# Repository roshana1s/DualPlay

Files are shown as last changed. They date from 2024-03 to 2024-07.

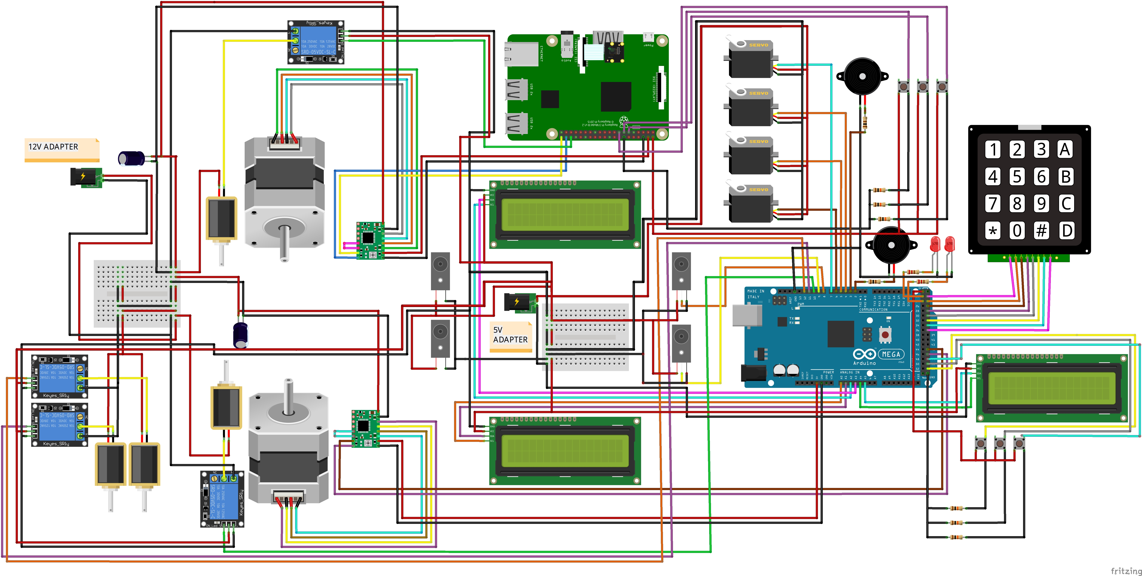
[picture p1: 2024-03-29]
Components and designs/initial_project_components.jpg

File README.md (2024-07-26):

# DualPlay
### The Ultimate Two-Side Air Hockey Experience with an Intelligent Opponent

dualplay_intro

## Introduction 📢
These days, as technology affects every part of our lives, hardware and entertainment combine to create a world of creative possibilities. The main attempt presented by this project is the creation  of an independent physical game that Blends traditional gaming with modern technology.

## Problem in Brief 🚩
1. No human interaction in traditional computer gaming.
   
2. Issues on social dynamics and physical health.
   
3. Traditional physical games require the presence of another player.

## Aim 🎯
Create an interactive multiplayer table game that combines the excitement of air hockey with innovative features.

## Objectives 🎯
1. Design and build the game with two game modes including an autonomous gameplay mode.
   
3. Ensure an enjoyable experience regardless of player availability.

## Game Modes 🎮
### 1. Human vs Human
Two players control paddles using two remotes.

### 2. Human vs AI Player
Human player controls the paddle using a remote and the paddle of the AI player autonomously controlled according to the ball movement by the system.

## Intelligent Features 🧠
1. When the game mode is “Human vs AI”, AI player’s paddle controlled autonomously by tracking the ball and the AI paddle real-time.

2. When a goal is scored, it will detect autonomously, and scores will be updated according to it.

3. After a goal is scored, ball will be redeployed back to the play area autonomously without human intervention.

## Technologies Used 🖥️

### 1. Computer Vision 👁️‍🗨️
  
We implemented a real-time computer vision algorithm using OpenCV in Python to track the colors of the ball and the AI player's paddle. We used HSV color space for this. This allowed us to accurately identify and monitor their positions throughout the game. This computer vision algorithm is executed on Raspberry pi 4 board.



### 2. Arduino Mega and Uno

Arduino Mega controls Green Player side (Human player) and Uno controls Red player side (Human/AI). Game setup LCD, Keypad, Score update LCDs, IR modules, Redeploy servo motors are controlled by Mega. Both boards programmed using C++ and Arduino IDE.

### 3. Serial Communication

We used Serial Communication to communicate between Raspberry pi and two Arduino boards. Arduino boards plugged into raspberry pi through USB ports. 

## Resources Required - Hardware ⚙️

Raspberry pi 4 model B

Arduino Mega

Arduino Uno

Nema 17 Stepper motor *2

180-degree SG90 Servo motor *2

360-degree SG90 continuous Servo motor *2

A4988 Stepper Motor Driver *2

12V 30A power supply

Obstacle Avoidance IR module *2

LCD screen with I2C module *3

Keypad

Limit switch *4

Buck converter *2

Solenoid with Relay module *2

## Resources Required - Software 👨🏽‍💻

Arduino IDE

Geany editor

Tinkercad

SolidWorks

fritzing

## Block Diagram



## Our Team
1. Epasinghe S K
2. Helapalla K O R I
3. Dhananjana R A
4. Nimraka T M N
5. Randinu L L

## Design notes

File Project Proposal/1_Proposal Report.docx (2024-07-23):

CM 1900- Intelligent Machines Inspirational Project

PROJECT PROPOSAL REPORT

Level 01

DualPlay

The Ultimate Two-Side Air Hockey Experience with an Intelligent Opponent

Examiner - Mr. B. H. Sudantha

Submitted by:

225511E - Epasinghe S.K

225520F - Helapalla K.O.R.I

225507X - Dhananjana R.A

225529P - Nimraka T.M.N

225537M - Randinu L.L

Bachelor of Artificial Intelligence

Faculty of Information Technology

University of Moratuwa

# 1. Introduction

These days, as technology affects every part of our lives, hardware and entertainment combine to create a world of creative possibilities. The main attempt presented by this project is the creation of an independent physical game that blends traditional gaming with modern technology. Designed specifically to give players a dynamic experience. Our game named “DualPlay” uses robotics, sensors, and intelligent algorithms to deliver a level of excitement and engagement never seen before.

## 1.1 Problem in Brief

When it comes to the traditional model of computer gaming, it involves playing video games through a computer interface without interacting with other players. Playing these kinds of games for extended periods of time can have negative impacts on social dynamics and physical health. On the other hand, multiplayer, traditional physical games require the presence of another player. In response to these worries, we suggest incorporating the hybrid game "Dual Play," which aims to promote player interaction while also providing independent player-versus-artificial intelligence (AI) features. This invention reduces the limitations that come with playing traditional games by enabling players to engage in gameplay without the need for human players.

## 1.2 Significance of study

This game promotes innovation in gaming technology by providing the player with a hybrid option of playing against a player as well as an autonomous opponent, promoting social interactions while providing the ability to play the game without a human opponent when required. This defines the adaptability of this game to provide entertainment irrespective of the situation. “DualPlay” promotes physical interaction of a player omitting the issues in the traditional computer games.

## 1.3 Aim and Objectives

Aim

The project aims to create an engaging and interactive multiplayer table game that combines the excitement of air hockey with innovative features such as autonomous gameplay modes and customizable gameplay options. The game, titled " DualPlay: The Ultimate Two-Side Air Hockey Experience with an Intelligent Opponent", will provide players with a unique and enjoyable gaming experience that encourages social interaction, strategic thinking, and friendly competition.

Objectives

- To design and build an upgraded version of air hockey game with two game modes: Human vs Human and Human vs Intelligent system.
- To provide an entertaining and enjoyable game that promotes relaxation and mental stress relief.
- To Create a multiplayer experience that encourages social interaction and friendly competition among players.
- To encourage Human Players to Engage in Duels, Challenging and Defeating the Intelligent System player for Ultimate Victory.
- To implement autonomous gameplay modes to accommodate varying numbers of players and ensure an enjoyable experience regardless of player availability.
- To enhance gameplay with visual cues through LCD displays to indicate scores and an integrated sound system for an immersive experience.
- To develop user friendly interfaces for selecting game modes, selecting difficult levels, selecting number of rounds, and keeping track of scores.

# 1. Literature Study

Air Hockey is an interactive and an exciting game for individuals to play during their free time to entertain themselves. It is table game in which two players attempt to score points by using a handheld paddle to shoot a plastic disk across a surface with minimal friction into the opponent's goal [1]. But this game limits at least two players to be present in order to play a game. DualPlay stands out as a unique game which can control one paddle autonomously using computer vision techniques. This can eliminate the limitation where two or more players must be present in order to play a game successfully since only one player can play by controlling the designated paddle while the other paddle functions autonomously.

Players in an Air Hockey game does not receive points or prizes for winning. However, with DualPlay, a player's point scoring may be easily detected and recorded on the LCD screen thanks to the IR break beam sensor. When the game is over, it will also play a victory sound to cheer up the winner.

# 2. Proposed Solution

Our proposed solution, the DualPlay air hockey game, represents a notable advancement from traditional air hockey games. One key feature is the option for human players to compete against either another human player or an intelligent system. This intelligent system utilizes computer vision with OpenCV color tracking and contours detection to dynamically track the ball's movements to get the real-time location of the ball, providing a substantial challenge for human players. Human interaction is facilitated through a user-friendly remote control with three buttons for easy paddle manipulation. Our system sets itself apart with well-organized game modes with different difficulty levels, a real-time score updating system, and innovative ball redeploying mechanisms, establishing the DualPlay system as a distinguished and engaging choice in the air hockey market.

## 2.1 Features of the Proposed Solution

1. Game Initialization: The LED displays show the main menu with the available gameplay modes and difficulty levels.
2. Mode Selection: Player(s) approaches the table and selects their desired gameplay mode using the keypad on the table.

• Available modes include,

- Human vs Intelligent system (1v1)
- Human vs Human (1v1)

• The system will then prompt for the number of points required for a player to win.

3. Player Setup:

• Human vs Intelligent system (1v1) – A human player takes their position at one side of the table and controls their paddle using the corresponding wired remote. The opposing side is autonomously guided by the intelligent system.

• Human vs Human (1v1) – Both human players take their respective positions at the table and control their paddles using individual wired remotes for each side.

4. Ball Placement: The ball will be automatically launched onto the table from one player's side, initiating the start of the game.
5. Game Start:

• Players use their remote controls to move their paddles and start hitting the ball. In cases where the intelligent system is participating, it autonomously guides its paddle by tracking the ball’s position.

• The game begins, and players try to hit the ball into their opponent's goal to score points.

6. Scoring a Goal:

• When a player successfully hits the ball into their opponent's goal, a point is scored.

• The LCD displays update the score, and the sound system emits a celebratory sound to mark the achievement.

7. Ball Reset:

• Following a scored point, the ball is automatically launched onto the table from the side of the player who did not score the point.

8. Score Tracking:

• The LCD displays update the scores for each player in real-time.

• Players can easily see the current score without interrupting the game.

9. Autonomous Gameplay (Human vs Intelligent system (1v1)):

• Here, the system controls one side of the table.

•The Intelligent opponent(system) uses computer vision to track the ball’s position to move the paddle correctly to provide a challenge to the player.

10. Match Completion:

• The game proceeds until one player achieves the predefined winning score.

11. Game Over:

• The game concludes when a player wins the match.

• The LCD displays show the final scores and show who is the winner, and the sound system produces a victory sound.

12. Reset for New Match:

• Players can choose to start a new match, change modes, or end the session.

13. Power Down:

• When the gaming session is complete, the game can be powered down.

• Scores and settings are reset for the next session.

## 2.2 Nature of the Solution

Input

Process

Output

If the system is playing, Track the color of the ball using computer vision algorithms to get the real-time location of the ball and control the intelligent system’s paddle according to the location of the ball. If the human is playing, control the paddle according to user inputs.

Raspberry pi 3 model B

Real-time video capture

Camera

Control the paddle

Belt driven linear paddle system with Nema 17 stepper motor and a solenoid lock

User press push buttons

Push Buttons

(Wired Remote)

Give a signal when the game starts with the game mode and difficulty level or when a round starts

Display game modes, difficulty levels and

Mode selection LCD screen

Arduino Mega

User input

Select the game mode, difficulty level and number of rounds according to the user input.

number of rounds

Keypad

Belt driven linear paddle system with Nema 17 stepper motor and a solenoid lock

User press push buttons

Push Buttons

(Wired Remote)

Control the user's paddle based on input received from the push buttons on the remotes.

Control the paddle

IR Break Beam Sensor

When the ball enters a hole, update the scores on the LCD screens accordingly and activate the buzzer to play the round-winning sound.

Game score updating system with lcd screens and buzzers, and ball redeploy system with servo motors

Whether the ball enters a hole or not

Update scores and redeploy the ball

Figure 01: Block diagram of the input, process, and output

## 2.3 Solution Design

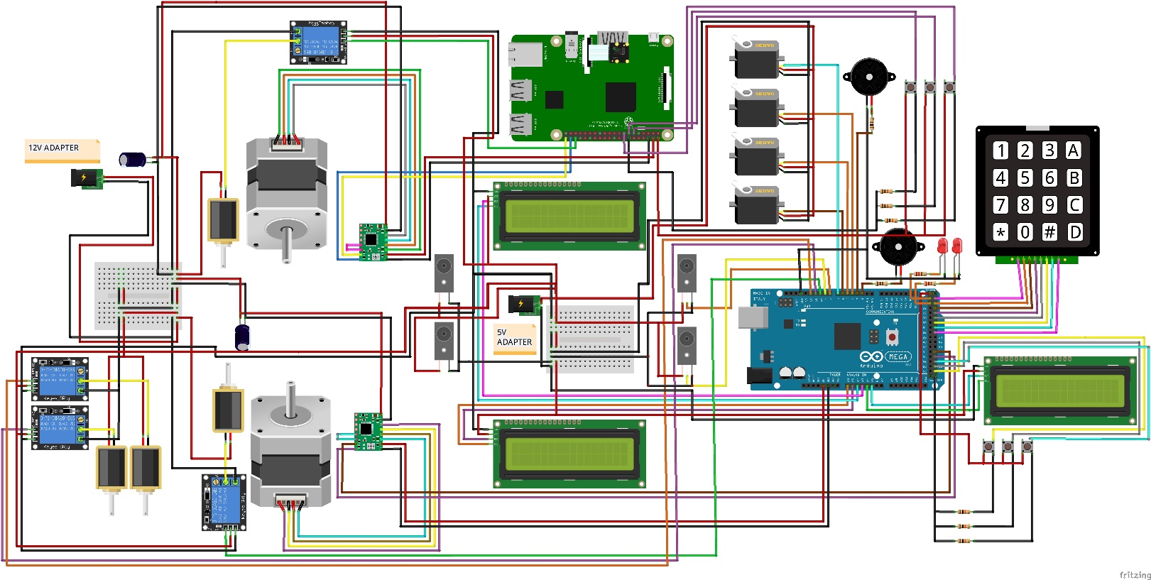
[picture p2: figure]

Figure 02: Connection of components

Scores

Paddle

Ball

Hole

Camera

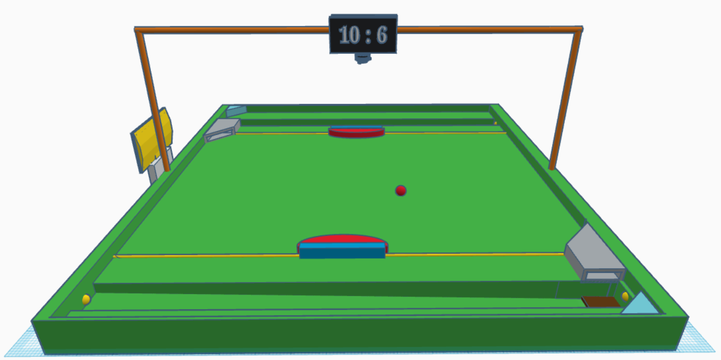
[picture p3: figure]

50 cm

50 cm

IR Break Beam Sensor

Ball Redeploy Mechanism

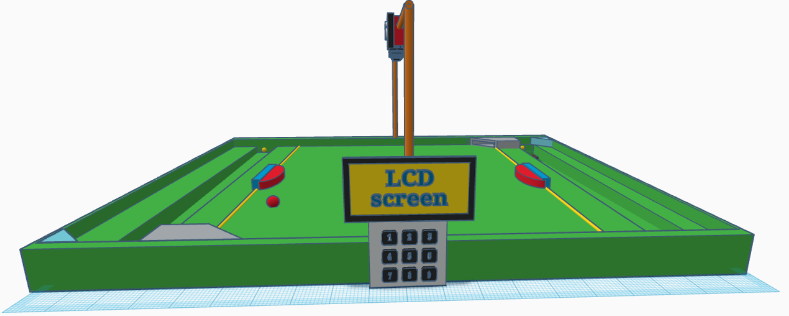
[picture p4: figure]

Mode Selection LCD Screen

Keypad

Figure 03 & 04: A graphical or 3D view of the solution.

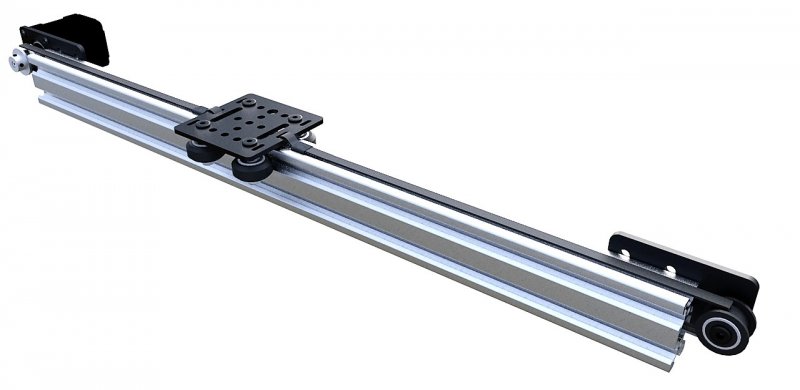
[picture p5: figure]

NEMA 17 stepper motor

Belt

Paddle

Pulley

Figure 05: Paddle move mechanism [2].

## 2.4 Resources

Item name | Price | No. of items | Total (LKR)
Raspberry Pi 3 Model B | 21650 | 1 | 21650
Arduino Mega | 5800 | 1 | 5800
Kingston MicroSD 32GB | 1850 | 1 | 1850
5V 3A Micro USB Power Adapter (Raspberry Pi) | 1050 | 1 | 1050
Tactile Push Button 12x12x7.3mm | 20 | 6 | 120
Servo Motor Plastic Wheel MG90 Full Set | 450 | 2 | 900
Servo Motor Plastic Wheel SG90 Full Set Normal | 380 | 2 | 760
4x4 Matrix Array Keypad | 270 | 1 | 270
1602 16x2 Blue Backlight LCD Display | 360 | 3 | 1080
IIC/I2C/TWI/SPI Serial Interface Board Module Port for 1602 LCD Display PCF8574T | 230 | 3 | 690
Camera Module v1.3 5MP 1080p 720p for Raspberry Pi 3 and 2 | 1350 | 1 | 1350
15-Pin Ribbon Cable 50cm Flex CSI Raspberry Pi Camera | 100 | 1 | 100
17HS8401 NEMA 17 Stepper with wire 0.52Nm (D Shaft 5mm) | 2900 | 2 | 5800
1Kg 3D Printer Filament | 5000 | 1 | 5000
A4988 Stepper Motor Driver for CNC 3D Printer | 350 | 2 | 700
30 Teeth Timing Pulley (5mm Bore) | 560 | 2 | 1120
Brown GT2 6mm Timing Belt (Anti-Slip Toothed Cloth, Rubber with Fiberglass) Per 1m | 430 | 2.5m | 1075
IR Break Beam Sensor 5mm LED | 690 | 2 | 1380
Plywood board (50cm * 50cm) | 1000 | 1 | 1000
Solenoid switch | 1450 | 4 | 5800
2020 t slot aluminum extrusion 1m | 2450 | 1 | 2450
Linear system paddle and supporters | 3000 | 2 | 6000
5VDC 2 Way 2 Channel Relay Module with Coupling Protection | 300 | 2 | 600
SHD2210 Active Piezo Buzzer 3-24VDC 22x10mm | 170 | 2 | 340
12V 20A SMPS Power Supply Metal Casing | 3100 | 1 | 3100
Net Amount | 69390 LKR

## 3.5 Workload Matrix

Registration Number | Assigned Responsibilities
225511E | Program servo motors for ball lift mechanism and program solenoid to strike the ball. (Ball redeploy mechanism in one side) Program two push buttons to get user inputs and program Nema 17 motor for the human play paddle movement according to push button inputs. (One side) Program the mode selection lcd screen to show “A match is ongoing” during a match.
225520F | Program the camera to detect and get the location of the ball and program Nema 17 motor for the system’s paddle movement and program solenoid with relay module to strike the ball for system play. Program two lcd screens, LEDs and buzzers to show the winner and the looser after a match. Make the connection between Arduino and raspberry pi.
225507X | Program one push button to get user input and program solenoid with relay module to strike the ball for the human play according to push button inputs. (One side) Program the keypad and mode selection lcd screen to select game modes, difficulty level and to get number of rounds from the user and program LEDs and buzzers to indicate the start of a match.
225529P | Program two push buttons to get user inputs and program Nema 17 motor for the human play paddle movement according to push button inputs. (One side) Program servo motors for ball lift mechanism and program solenoid to strike the ball. (Ball redeploy mechanism in one side) Program IR beam break sensor in one side.
225537M | Program IR beam break sensors, two lcd screens to display points of players and program buzzers and LEDs to show a point is scored by a player (One side) Program one push button to get user input and program solenoid with relay module to strike the ball for the human play paddle according to push button inputs. (One side)

# 4. References

[1] | "merriam-webster," 2 2 2024. [Online]. Available: https://www.merriam-webster.com/dictionary/air%20hockey.
[2] | "open builds part store," 10 1 2024. [Online]. Available: https://openbuildspartstore.com/v-slot-nema-17-linear-actuator-bundle-belt-driven/ .
[3] | A. TEAM, "arduino.cc," [Online]. Available: https://blog.arduino.cc/2018/10/29/linear-movement-with-arduino-and-3d-printing/. [Accessed 10 1 2024].
[4] | Felipe, "Computer vision engineer," [Online]. Available: https://www.youtube.com/watch?v=eDIj5LuIL4A . [Accessed 27 12 2023].
[5] | "Mechanical Design Masters," [Online]. Available: https://youtu.be/ve9M8d6KfdI?si=8PxCvQbe-xPVnI0p. [Accessed 20 12 2023].
[6] | "OpenCV," [Online]. Available: https://docs.opencv.org/3.4/df/d9d/tutorial_py_colorspaces.html. [Accessed 27 12 2023].
[7] | "OpenCV," [Online]. Available: https://docs.opencv.org/3.4/da/d97/tutorial_threshold_inRange.html. [Accessed 27 12 2023].
[8] | "OpenCV," [Online]. Available: https://docs.opencv.org/4.x/d3/d05/tutorial_py_table_of_contents_contours.html. [Accessed 27 12 2023].

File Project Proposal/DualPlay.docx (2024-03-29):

CM 1900 - Intelligent Machines Inspirational Project

B.Sc.(Hons) Artificial Intelligence

Group 01

Admission No | Name
225511E | Epasinghe S.K
225520F | Helapalla K.O.R.I
225507X | Dhananjana R.A
225529P | Nimraka T.M.N
225537M | Randinu L.L

DualPlay

The Ultimate Two-Side Air Hockey Experience with an Intelligent Opponent

# Introduction:

The project aims to create an engaging and interactive multiplayer table game that combines the excitement of air hockey with innovative features such as autonomous gameplay modes and customizable gameplay options. The game, titled " DualPlay: The Ultimate Two-Side Air Hockey Experience with an Intelligent Opponent", will provide players with a unique and enjoyable gaming experience that encourages social interaction, strategic thinking, and friendly competition.

## Game Modes:

- Human vs Intelligent player(system)
- Human vs Human

# System objectives:

- Provide an entertaining and enjoyable game that promotes relaxation and mental stress relief.
- Create a multiplayer experience that encourages social interaction and friendly competition among players.
- Encourage Human Players to Engage in Duels, Challenging and Defeating the Intelligent System player for Ultimate Victory
- Implement autonomous gameplay modes to accommodate varying numbers of players and ensure an enjoyable experience regardless of player availability.
- Enhance gameplay with visual cues through LCD displays to indicate scores and an integrated sound system for an immersive experience.
- Develop user-friendly interfaces for selecting gameplay modes and keeping track of scores.

# How The Game Works:

The game supports multiple play modes to cater to different numbers of players.

1. Game Initialization:

- The LED displays show the main menu with the available gameplay modes.

2. Mode Selection:

- Player(s) approach the table and select their desired gameplay mode using the buttons on the table.
- Available modes include,
    - Human vs Intelligent system (1v1)
    - Human vs Human (1v1)
- The system will then prompt for the number of points required for a player to win.

3. Player Setup:

- Human vs Intelligent system (1v1) – A human player takes their position at one side of the table and controls their paddle using the corresponding wired remote. The opposing side is autonomously guided by the intelligent system.
- Human vs Human (1v1) – Both human players take their respective positions at the table and control their paddles using individual wired remotes for each side.

4. Ball Placement:

- The ball will be automatically launched onto the table from one player's side, initiating the start of the game.

5. Game Start:

- Players use their remote controls to move their paddles and start hitting the ball. In cases where the intelligent system is participating, it autonomously guides its paddle by tracking the ball’s position.
- The game begins and players try to hit the ball into their opponent's goal to score points.

6. Scoring a Goal:

- When a player successfully hits the ball into their opponent's goal, a point is scored.
- The LCD displays update the score, and the sound system emits a celebratory sound to mark the achievement.

7. Ball Reset:

- Following a scored point, the ball is automatically launched onto the table from the side of the player who did not score the point.

8. Score Tracking:

- The LCD displays update the scores for each player in real-time.
- Players can easily see the current score without interrupting the game.

9. Autonomous Gameplay (Human vs Intelligent system (1v1)):

- Here, the system controls one side of the table.
- The Intelligent opponent(system) uses computer vision to track the ball’s position to move the paddle correctly to provide a challenge to the player.

10. Match Completion:

- The game proceeds until one player achieves the predefined winning score.

11. Game Over:

- The game concludes when a player wins the match.
- The LCD displays show the final scores and show who is the winner, and the sound system produces a victory sound.

12. Reset for New Match:

- Players can choose to start a new match, change modes, or end the session.

13. Power Down:

- When the gaming session is complete, the game can be powered down.
- Scores and settings are reset for the next session.

# System Components and Sensors

Item name | Price | No. of items | Total
Raspberry Pi 3 Model B * | 21650 | 1 | 21650
Arduino Mega | 5800 | 1 | 5800
Kingston MicroSD 32GB | 1900 | 1 | 1900
5V 3A Micro USB Power Adapter (Raspberry Pi) | 1050 | 1 | 1050
DS-212 Green 16mm Round Metal Push Button Momentary Switch | 100 | 4 | 400
DS-212 Red 16mm Round Metal Push Button Momentary Switch | 100 | 2 | 200
Continuous Rotation SG90 Servo Motor Plastic Wheel Full Set Normal (360 degrees) | 350 | 4 | 1400
4x3 Matrix Array Keypad Switch Module | 750 | 1 | 750
1602 16x2 Blue Backlight LCD Display | 360 | 3 | 1080
IIC/I2C/TWI/SPI Serial Interface Board Module Port for 1602 LCD Display PCF8574T | 230 | 3 | 690
Camera Module v1.3 5MP 1080p 720p for Raspberry Pi 3 and 2 | 1350 | 1 | 1350
15-Pin Ribbon Cable 50cm Flex CSI Raspberry Pi Camera | 100 | 1 | 100
17HS8401 NEMA 17 Stepper with wire 0.52Nm (D Shaft 5mm) | 2900 | 2 | 5800
Creality Ender EN-PLA White 1.75mm 1Kg 3D Printer Filament | 5600 | 1 | 5600
A4988 Stepper Motor Driver for CNC 3D Printer | 350 | 2 | 700
GT2 20T 20 Teeth Timing Pulley (5mm Bore) 20TB5W6 Silver | 180 | 2 | 360
Brown GT2 6mm Timing Belt (Anti-Slip Toothed Cloth, Rubber with Fiberglass) Per 1m | 430 | 3m | 1290
IR Break Beam Sensor 5mm LED | 690 | 2 | 1380
Plywood board | 2000 | 1 | 2000
Solenoid switch | 1000 | 2 | 2000
Net Amount | 49650

# System Functions

## 1. Wired Remotes

Each wired remote is equipped with three push buttons:

    - One to move the paddle to the left.
    - One to move the paddle to the right.
    - One to push the ball.

## 2. Table (Main System)

### Ball Tracking

When the Intelligent system is in play, the system employs computer vision algorithms from the OpenCV library to track the real-time color of the ball. By utilizing computer vision algorithms to track the ball's color, the system can dynamically identify the ball's position in real-time, allowing the system to adjust the paddle's movement accordingly.

### Paddle Move Mechanism

The paddle move mechanism utilizes a NEMA 17 stepper motor paired with an A4988 driver, and a 20-tooth timing pulley connected to a timing belt. As the stepper motor rotates, it drives the timing pulley, causing linear motion in the attached timing belt. This motion is then transferred to the air hockey paddle, enabling precise and controlled movement on the playing surface.


Belt

Paddle

Pulley

NEMA 17 stepper motor

An example for paddle move mechanism (actual design may differ)

### Ball Pushing Mechanism

The pushing mechanism involves a continuous servo motor equipped with a rack and pinion gear system. This setup transforms the rotational motion of the servo into linear motion. When activated, the servo engages the rack and pinion gears, swiftly converting rotational energy into a sudden linear push. This mechanism is specifically designed to impart a quick and precise force to propel the ball during gameplay.

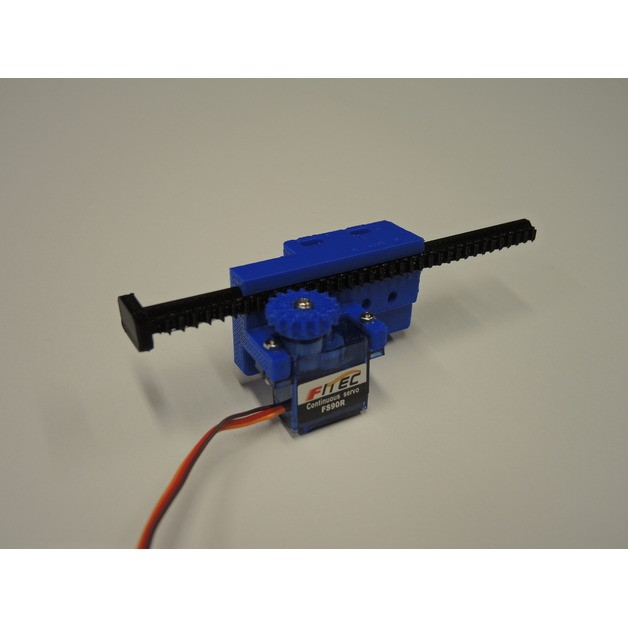
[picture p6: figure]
Jual Linear Servo Actuators - Kota Bekasi - Ednic Indonesia | Tokopedia

Rack

Servo motor

Pinion gear

An example for Ball pushing mechanism (actual design may differ)

### Score tracking

In our scoring system, an IR Break Beam Sensor is employed to detect whether the ball has entered the goal. When a player scores a point, the IR Break Beam Sensor registers this event and sends the signal to a Raspberry Pi. Subsequently, the Raspberry Pi communicates the scoring information to an Arduino Uno board, ensuring real-time score updates during gameplay.

### Ball Redeploy Mechanism

A built-in inclined plane in the hole, guides the ball to the right corner within the goal. Using a servo motor and a rack and pinion mechanism, the ball is lifted to table level. Once elevated, the same mechanism generates a pushing effect, redeploying the ball back into the play area. This simple yet effective system ensures a smooth and consistent ball redeployment process after scoring.

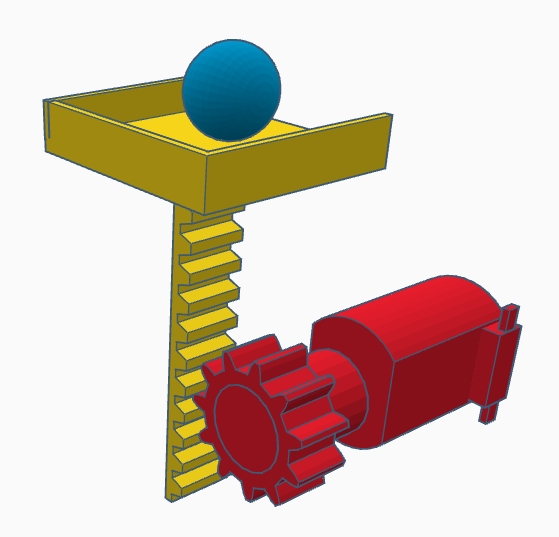
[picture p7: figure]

continuous Servo motor

(static position)

An example for Ball lifting mechanism (actual design may differ)

# Block Diagram

Camera Module

Push Buttons

LCD screens

(scores)

12C modules

Stepper Motors

Raspberry PI

Arduino UNO

Buzzers

A4988

LEDs

Servo motors

Mode selection LCD screen

12C module

IR Break Beam Sensors

Keypad

# Design

Scores


Camera

Ball Redeploy Mechanism

Hole

Ball

Paddle

IR Break Beam Sensor


Mode Selection LCD Screen

Keypad

# References

OpenCV Documentation

- https://docs.opencv.org/3.4/df/d9d/tutorial_py_colorspaces.html
- https://docs.opencv.org/3.4/da/d97/tutorial_threshold_inRange.html
- https://docs.opencv.org/4.x/d3/d05/tutorial_py_table_of_contents_contours.html

OpenCV YouTube Tutorial

- https://www.youtube.com/watch?v=eDIj5LuIL4A

Mechanisms for converting Rotational Motion into Linear

- https://youtu.be/ve9M8d6KfdI?si=8PxCvQbe-xPVnI0p

Other Links –

- https://blog.arduino.cc/2018/10/29/linear-movement-with-arduino-and-3d-printing/
- https://openbuildspartstore.com/v-slot-nema-17-linear-actuator-bundle-belt-driven/

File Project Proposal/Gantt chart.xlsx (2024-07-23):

Task | Start Date | End Date | Duration
Identify problem and propose solution | 2023-12-22 | 2023-12-29 | 7
Conduct research | 2023-12-30 | 2024-01-04 | 5
Finalize project design and obtain approval | 2024-01-05 | 2024-01-12 | 7
Develop computer vision algorithm for ball tracking | 2024-01-01 | 2024-01-20 | 19
Establish connection between Raspberry Pi and Arduino | 2024-02-07 | 2024-02-14 | 7
Implement LCD screen and keypad for game setup | 2024-03-13 | 2024-03-30 | 17
Implement linear actuator | 2024-02-14 | 2024-03-20 | 35
Integrate solenoid with relay for ball striking | 2024-02-16 | 2024-02-23 | 7
Develop remote input for solenoid control | 2024-02-23 | 2024-03-02 | 8
Develop remote input for linear actuator (paddle) control | 2024-03-16 | 2024-04-10 | 25
Develop autonomous solution for solenoid control | 2024-05-02 | 2024-05-10 | 8
Develop autonomous solution for linear actuator control | 2024-04-06 | 2024-04-22 | 16
Implement goal counter | 2024-04-06 | 2024-04-22 | 16
Integrate buzzers and LEDs | 2024-04-22 | 2024-04-25 | 3
Implement ball redeploy mechanism | 2024-05-01 | 2024-05-10 | 9
Finalize 3D parts design and initiate printing | 2024-04-25 | 2024-05-10 | 15
Implement second linear actuator (paddle) and solenoid | 2024-04-22 | 2024-05-10 | 18
Assemble all parts and complete project | 2024-04-22 | 2024-06-02 | 41

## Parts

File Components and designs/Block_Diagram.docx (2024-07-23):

If the AI player is playing, Track the color of the ball and paddle using computer vision algorithms to get the real-time location of the ball and the paddle.

Raspberry pi 4 model B

Real-time video capture

Camera

Control the paddle

Arduino Uno

Get signals from raspberry pi according to locations of the ball and the paddle and control AI player’s paddle.

Belt driven linear paddle system with Nema 17 stepper motor and a solenoid lock

User press push

buttons

Control the user's paddle based on input received from the push buttons on the remotes.

Push Buttons

(Wired Remote)

Control the paddle

Game setup LCD Screen

number of rounds

Display game modes, difficulty levels and

Arduino Mega

User input

Select the game mode and enter the number of rounds according to the user input.

Keypad

Belt driven linear paddle system with Nema 17 stepper motor and a solenoid lock

User press push buttons

Push Buttons

(Wired Remote)

Control the user's paddle based on input received from the push buttons on the remotes.

Control the paddle

IR Module

When the ball enters a hole, update the scores on the LCD screens accordingly and activate the buzzer and activate Redeploy mechanism.

Game score updating system with lcd screens and buzzer, and ball redeploy system with servo motors

Whether the ball enters a hole or not

Update scores and redeploy the ball

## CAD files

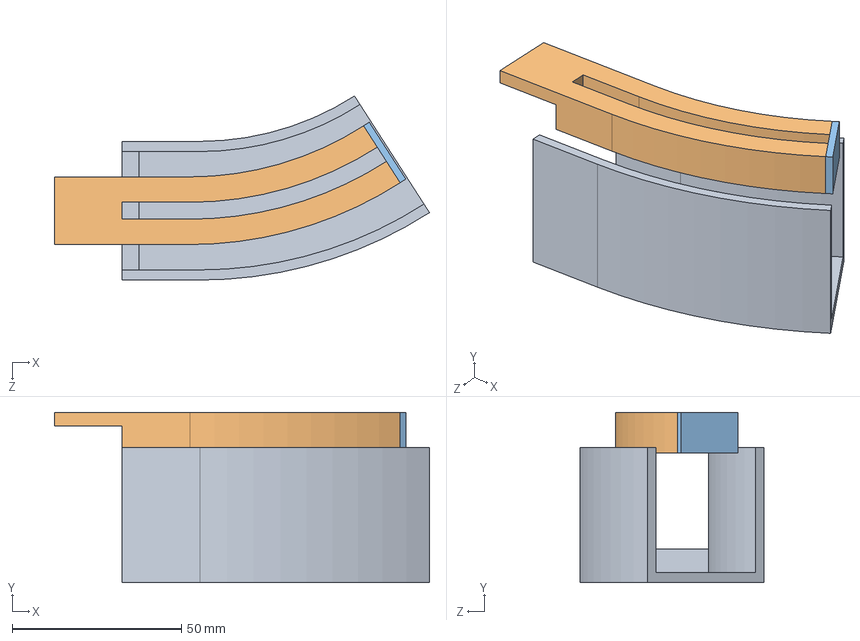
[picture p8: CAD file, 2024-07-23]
3d design/Redeploy-Push/Assem1.SLDASM
110.9 x 50.4 x 54.4 mm

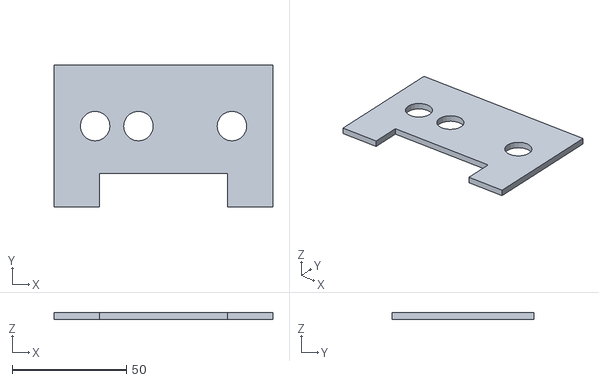
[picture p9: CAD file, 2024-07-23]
3d design/controller/controller1.stl
96.0 x 62.5 x 3.00

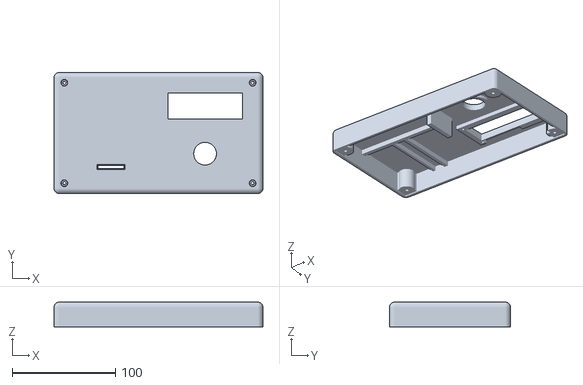
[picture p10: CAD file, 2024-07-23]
3d design/Game_Setup_LCD_and_Keypad/keypad cover.stl
202.0 x 117.0 x 24.0

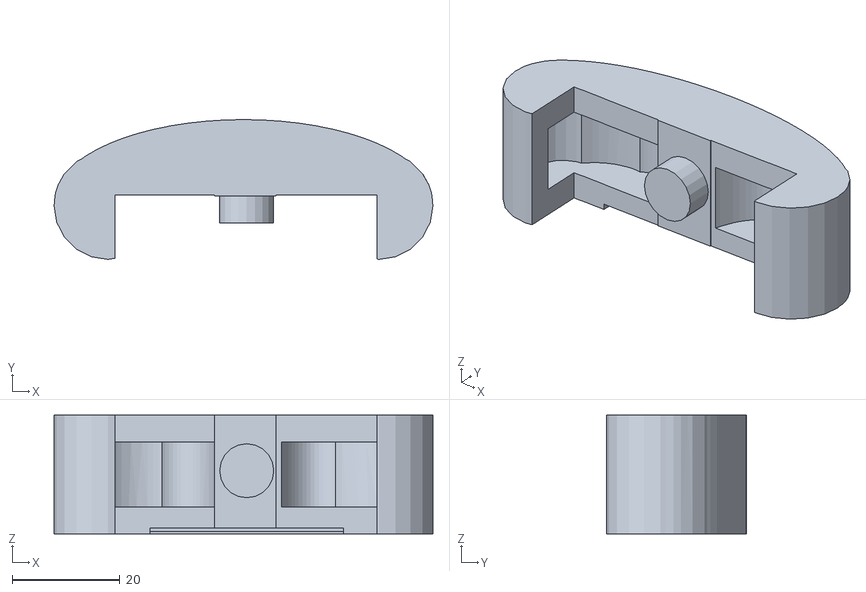
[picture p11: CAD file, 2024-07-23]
3d design/Paddle/strike1.stl
70.2 x 25.9 x 22.0

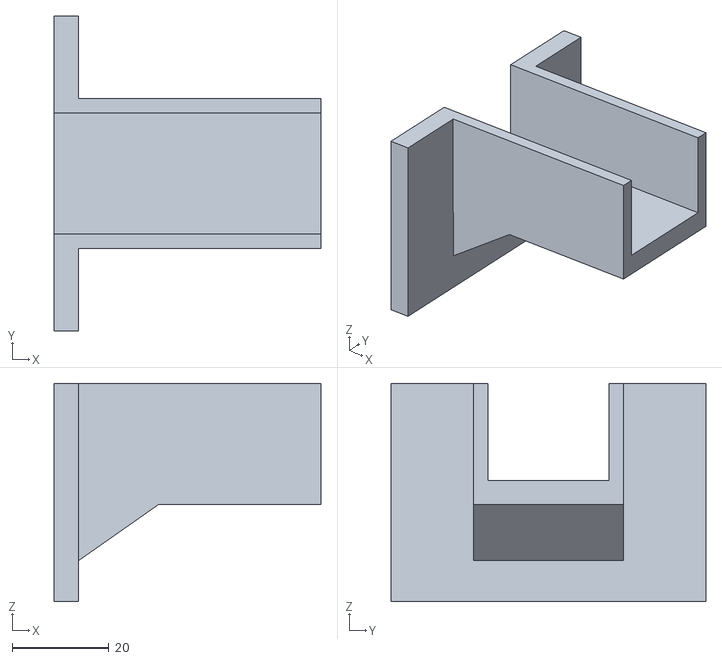
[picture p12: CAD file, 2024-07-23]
3d design/Rail_Support/railSup.stl
55.0 x 65.0 x 45.0

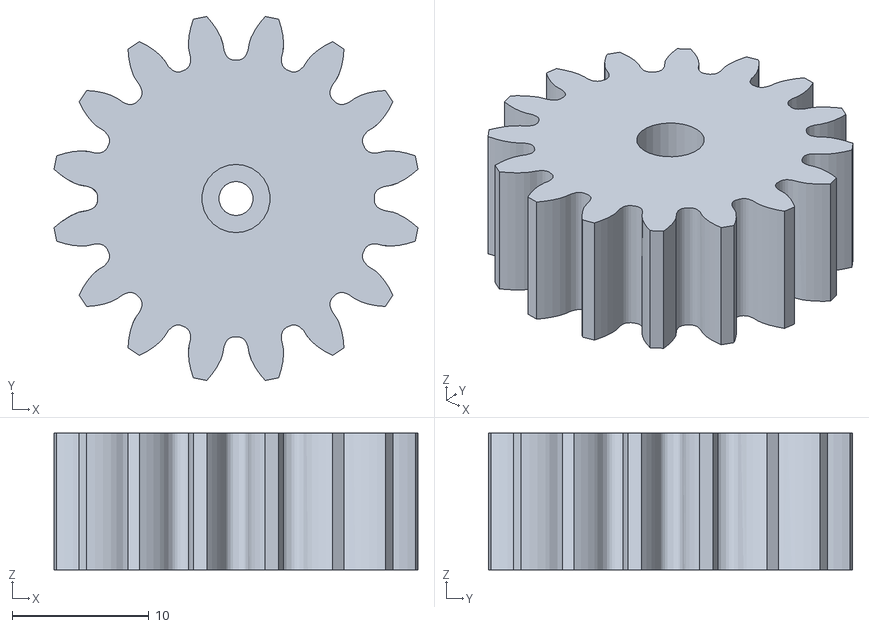
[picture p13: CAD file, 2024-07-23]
3d design/Redeploy-Lift/part5.stl
26.7 x 26.7 x 10.0

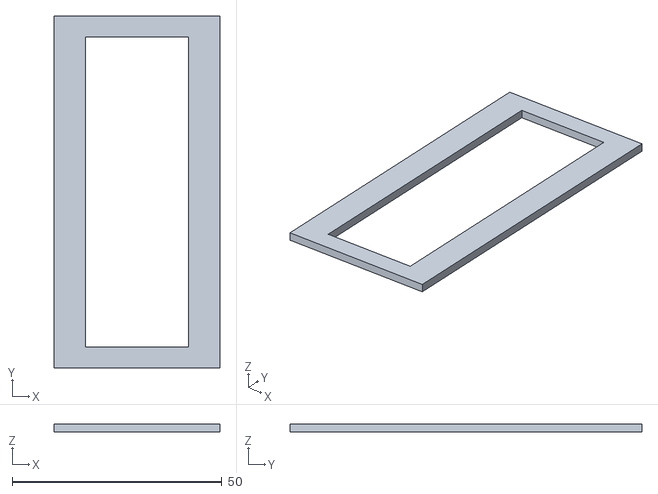
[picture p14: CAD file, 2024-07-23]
3d design/Score_Update_LCD/display2.stl
39.5 x 84.0 x 2.00

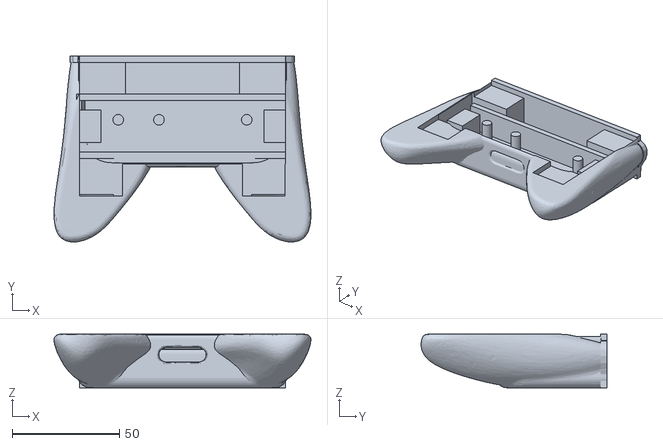
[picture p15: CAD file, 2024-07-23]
3d design/controller/controller2.stl
120.0 x 86.8 x 25.0

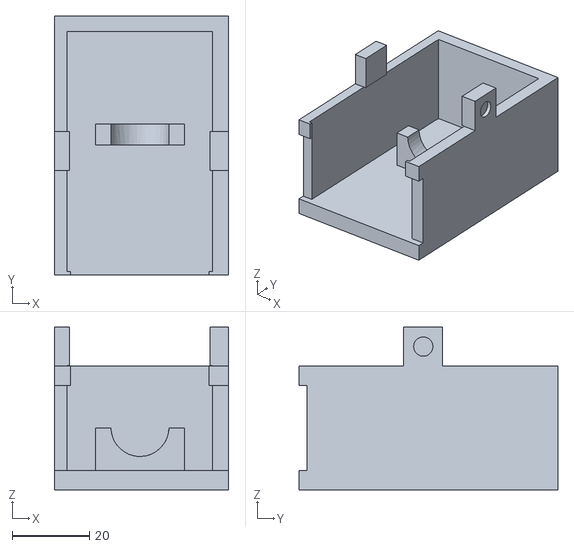
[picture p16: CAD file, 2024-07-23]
3d design/Paddle/paddle2.stl
45.0 x 66.9 x 42.0

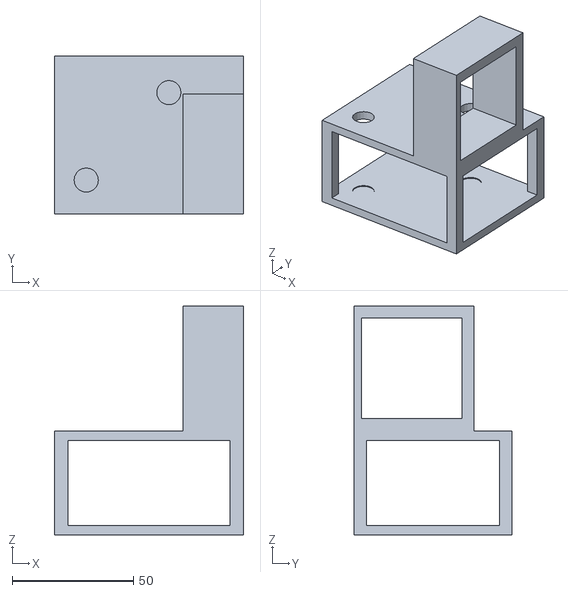
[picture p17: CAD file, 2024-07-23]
3d design/Rail_Support/support1.stl
78.0 x 65.0 x 94.5

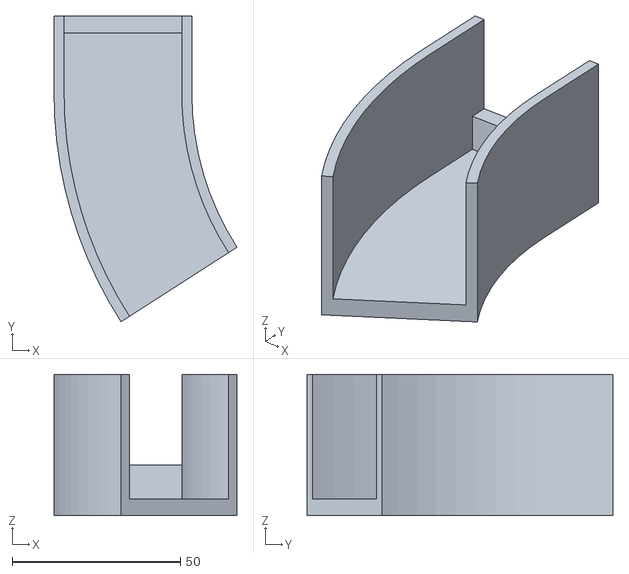
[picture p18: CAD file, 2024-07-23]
3d design/Redeploy-Lift/PART9.stl
54.4 x 90.9 x 42.0

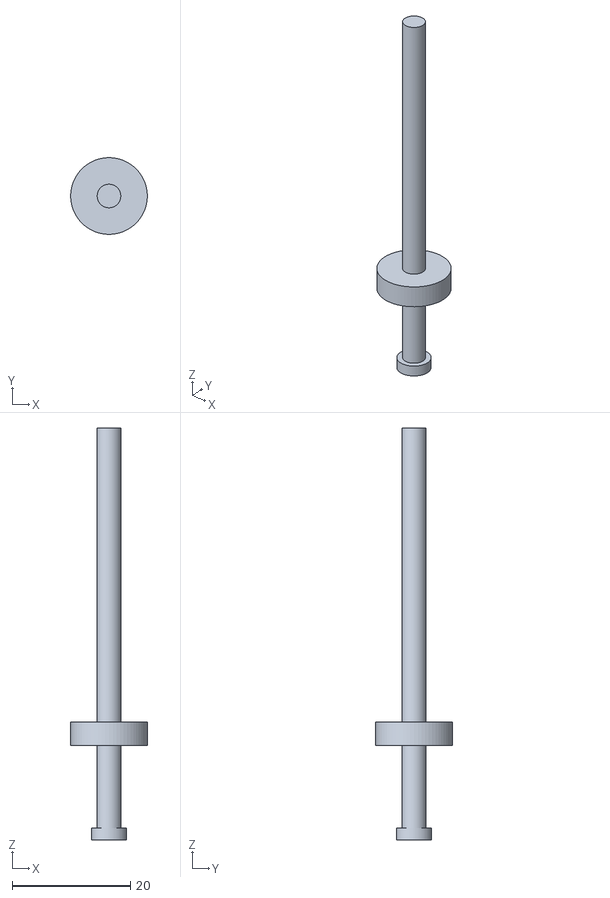
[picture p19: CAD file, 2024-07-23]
3d design/Redeploy-Push/PART6.stl
13.0 x 13.0 x 69.8

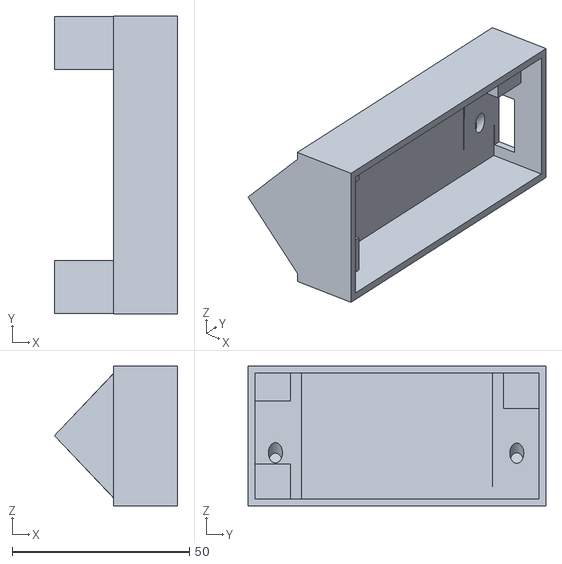
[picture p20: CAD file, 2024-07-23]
3d design/Score_Update_LCD/display1.stl
34.8 x 84.0 x 39.5

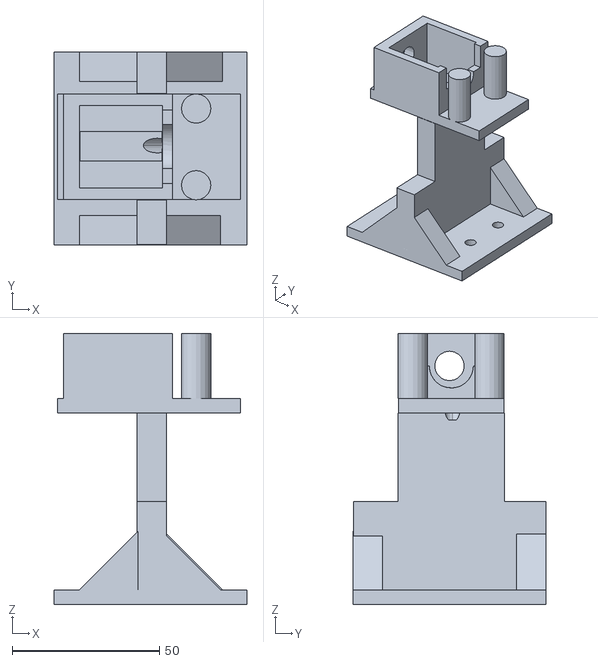
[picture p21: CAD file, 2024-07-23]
3d design/Paddle/paddle1.stl
65.5 x 65.6 x 92.0

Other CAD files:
3d design/Redeploy-Lift/lift3.stl
3d design/Redeploy-Push/PART2.stl
3d design/Paddle/strike11.stl
3d design/Redeploy-Lift/lift2.stl
3d design/Redeploy-Lift/PART9-1.stl
3d design/Redeploy-Lift/lift1.stl
3d design/Redeploy-Lift/lift4.stl
3d design/Redeploy-Lift/part4.stl
3d design/Redeploy-Push/PART1.stl
3d design/Redeploy-Push/PART3.stl
3d design/Redeploy-Push/PART4.stl
3d design/Redeploy-Push/PART5.stl
3d design/Redeploy-Push/PART7.STL
3d design/Redeploy-Push/PART8.stl
3d design/Redeploy-Push/Part7.SLDPRT
3d design/Redeploy-Push/Part8.SLDPRT
3d design/Redeploy-Push/Part9.SLDPRT

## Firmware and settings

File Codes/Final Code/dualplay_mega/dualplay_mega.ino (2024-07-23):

// DualPlay 

// Code for arduino Mega

#include <LiquidCrystal_I2C.h>
#include <Keypad.h>
#include <Servo.h>

// Obstacle Avoidance Sensor IR Infrared Module pins 
const int ir_red = 5, ir_green = 6;

// initial values and declare variables
int d, Nrounds, round_input, gm, com, gp, score, redScore = 0, greenScore = 0;

// A4988 motor driver direction and step pins
const int dirPin = 46, stepPin = 3;

const int stepsPerRevolution = 70;
const int debounceDelay = 50; // Debounce delay in milliseconds

// Pins for the remote
const int leftMove = 10, rightMove = 11, solenoid = 8;

// Pins for the relay and two limit switches
const int relay = 9, leftStop = 22, rightStop = 24;

// Pin for the active buzzer
const int buzzer = 2;

// Variables to messure time
unsigned long currentTime, b2Time = 0, b1Time = 0, solenoidTime = 0;

// delay between two steps of stepper motor
int del = 400, ir_value;

// 2D array for the 4x3keypad matrix
char keys[4][3] = {
	{'1','2','3'},
	{'4','5','6'},
	{'7','8','9'},
	{'*','0','#'}
};

// define row pins and column pins of the keypad
byte rowPins[4] = {28,30,32,34}; 
byte colPins[3] = {38,40,44}; 

//46 
// map keys
Keypad kpd = Keypad( makeKeymap(keys), rowPins, colPins, 4, 3 );


// define three lcd screens
LiquidCrystal_I2C lcd_gameSetup(0x27, 16, 2);
LiquidCrystal_I2C lcd_green(0x25 ,16, 2);
LiquidCrystal_I2C lcd_red(0x26, 16, 2);

// define four servo motors
Servo lift_green;
Servo push_green;
Servo lift_red;
Servo push_red;

/////////////////////////////////////////////////////////////////

// Function for Active buzzer
void sound_buzzer(){
    digitalWrite(buzzer, HIGH);
    delay(300);           
    digitalWrite(buzzer, LOW);
}

// welcome message
void wc_msg(){
    lcd_gameSetup.clear();
    lcd_gameSetup.setCursor(3, 0);
    lcd_gameSetup.print("Welcome to ");
    lcd_gameSetup.setCursor(4, 1);
    lcd_gameSetup.print("dualPlay"); 
}

// Select Play or Not
int gameplay(){
  lcd_gameSetup.clear();
  lcd_gameSetup.setCursor(0, 0);
  lcd_gameSetup.print("1)start");
  lcd_gameSetup.setCursor(0, 1);
  lcd_gameSetup.print("2)switch off");
  char key;
  while(1){
    key = kpd.getKey();
    if(key=='1' || key=='2'){
         sound_buzzer();
         break;
    }
  }
  return key-'0';
}

// Select the game mode
int game_mode(){
    lcd_gameSetup.clear();
    lcd_gameSetup.setCursor(2, 0);
    lcd_gameSetup.print("Select the");
    lcd_gameSetup.setCursor(3, 1);
    lcd_gameSetup.print("Game Mode");
    delay(1000);
    lcd_gameSetup.clear();
    lcd_gameSetup.setCursor(0, 0);
    lcd_gameSetup.print("1.Human vs Human");
    lcd_gameSetup.setCursor(0, 1);
    lcd_gameSetup.print("2.Human vs AI");
    char key;
    while(1){
      key = kpd.getKey();
      if(key=='1' || key=='2') {
        sound_buzzer();
        break;
      }
    }
    lcd_gameSetup.clear();
    if(key == '1'){
      lcd_gameSetup.setCursor(1, 0);
      lcd_gameSetup.print("You Selected");
      lcd_gameSetup.setCursor(1, 1);
      lcd_gameSetup.print("Human vs Human");
  }
  else if(key == '2'){
    lcd_gameSetup.setCursor(1, 0);
    lcd_gameSetup.print("You Selected");
    lcd_gameSetup.setCursor(1, 1);
    lcd_gameSetup.print("Human vs AI");
  }
  delay(1000);
  return key-'0';
}

// Select Number of Rounds
int rounds(){
  lcd_gameSetup.clear();
  lcd_gameSetup.setCursor(0, 0);
  lcd_gameSetup.print("{No of rounds}#");
  lcd_gameSetup.setCursor(0, 1);
  lcd_gameSetup.print("Enter(max 99): ");
  lcd_gameSetup.setCursor(14, 1);

  String number = "";
  while(1){
    char key;
    key =  kpd.getKey();
    if(isdigit(key) && number.length()<2){
      sound_buzzer();
      if(key == '0' && number.length()==0){
        continue;
      }else{
        lcd_gameSetup.print(key);
        number += String(key);
      }
    }
    else if(key=='#' && number.length()>=1){
      sound_buzzer();
      lcd_gameSetup.clear();
      lcd_gameSetup.setCursor(0, 0);
      lcd_gameSetup.print("No of rounds:");
      lcd_gameSetup.setCursor(13, 0);
      lcd_gameSetup.print(number);
      lcd_gameSetup.setCursor(0, 1);
      lcd_gameSetup.print("Game is ongoing");
      return number.toInt();
    }
    else if(key=='*' && number.length()>=1){
      sound_buzzer();
      number = number.substring(0, number.length() - 1);
      lcd_gameSetup.clear();
      lcd_gameSetup.setCursor(0, 0);
      lcd_gameSetup.print("{No of rounds}#");
      lcd_gameSetup.setCursor(0, 1);
      lcd_gameSetup.print("Enter(max 99): ");
      lcd_gameSetup.setCursor(14, 1);
      lcd_gameSetup.print(number);
    }
  }
}

// game setup function
void gameSetup(){
  gp = gameplay();
  if(gp==1){
    wc_msg();
    delay(1000);
    gm = game_mode();
    Nrounds = rounds();
    com = gm;
  }
  else{
    com = 0;
    lcd_gameSetup.clear();
    lcd_gameSetup.setCursor(1, 0);
    lcd_gameSetup.print("Switching Off!!!!");
    delay(4000);

    lcd_gameSetup.clear();
    lcd_green.clear();
    lcd_red.clear();

    lcd_gameSetup.setCursor(1, 0);
    lcd_gameSetup.print("GoodBye !!");
    lcd_green.setCursor(1, 0);
    lcd_green.print("GoodBye !!");
    lcd_red.setCursor(1, 0);
    lcd_red.print("GoodBye !!");
  }
}

// Function to clear serial buffer
void ClearSerial(){
  while (Serial.available() > 0) {
    Serial.read();
  }
}

// Function to check whther ir beam is intact or not
int breakbeam() { 
  // Small delay to avoid flooding the Serial Monitor
    if (!digitalRead(ir_red)) {
        // Serial.println("IR Beam is Broken - red");
        return 1;
    }else if (!digitalRead(ir_green)) {
        // Serial.println("IR Beam is Broken - Green");
        return 2;
   }else {
        // Serial.println("IR Beam is Intact");
        return 0;
    }
}

// Function to update score
void scoreDisplay(int red, int green){
    lcd_green.setCursor(0, 1);
    lcd_green.print("red: ");
    lcd_green.print(red);
    lcd_green.print(" Green: ");
    lcd_green.print(green);

    lcd_red.setCursor(0, 1);
    lcd_red.print("red: ");
    lcd_red.print(red);
    lcd_red.print(" Green: ");
    lcd_red.print(green);
}

void score_update(int score) {
    if (score == 1) {
        greenScore += 1;
    } else if (score == 2) {
        redScore += 1;
    }
    scoreDisplay(redScore, greenScore);

}

// Function to identify Button press for the paddle
void handleButtons()
{
  static unsigned long lastDebounceTime = 0;
  static int lastButtonState1 = HIGH;
  static int lastButtonState2 = HIGH;

  int buttonState1 = digitalRead(rightMove);
  int buttonState2 = digitalRead(leftMove);

  if (buttonState1 != lastButtonState1) {
    lastDebounceTime = currentTime;
  }

  if (buttonState2 != lastButtonState2) {
    lastDebounceTime = currentTime;
  }

  if ((currentTime - lastDebounceTime) > debounceDelay) {
    if (buttonState1 == LOW && digitalRead(rightStop)) {
      digitalWrite(dirPin, HIGH);
      runMotor();
    }
    if (buttonState2 == LOW && digitalRead(leftStop)) {
      digitalWrite(dirPin, LOW);
      runMotor();
    }
  }

  lastButtonState1 = buttonState1;
  lastButtonState2 = buttonState2;
}

// Function to run paddle
void runMotor()
{
  for (int x = 0; x < stepsPerRevolution; x++) {
    digitalWrite(stepPin, HIGH);
    delayMicroseconds(del);
    digitalWrite(stepPin, LOW);
    delayMicroseconds(del);
  }
}

// Function to identify button input to solenoid and strike the ball
void handleSolenoid()
{
  if (currentTime - solenoidTime >= 10) {
    solenoidTime = currentTime;
    if (digitalRead(solenoid) == LOW) {
      digitalWrite(relay, LOW);
    } else {
      digitalWrite(relay, HIGH);
    }
  }
}

// Function for the redeploy mechanism in the green side
void greenDeploy() {
  for (int pos = 90; pos <= 180; pos += 2) {
    push_green.write(pos);
    delay(5);  // Wait for 5 milliseconds for the servo to move
  }
  
  lift_green.write(75);  // Rotate counterclockwise
  delay(1600);     // Rotate for 2 seconds
  
  lift_green.write(90);  // Stop the servo
  delay(500);     // Wait for 1 second
  
  // Move the push_green servo back to 10 degrees
  push_green.write(90);
  delay(500);
  lift_green.write(110); // Rotate clockwise
  delay(1200);     // Rotate for 2 seconds
  
  lift_green.write(90);  // Stop the servo
}

// Function for the redeply mechanism in the red side
void redDeploy(){
  for (int pos = 85; pos <= 180; pos = pos + 1) {
    push_red.write(pos); // Sets 'push_red' servo to current 'pos' position
    delay(5);        // Waits for 5 milliseconds
  }

  lift_red.write(80);  // Rotate counterclockwise at full speed
  delay(1500);       // Rotate for 2 seconds
  lift_red.write(90); // Stop the servo
  push_red.write(85);
  delay(1000);
  lift_red.write(98); // Rotate clockwise at full speed
  delay(900);        

  lift_red.write(90);
}

// Function for run redeploy
void redeploy(int value){
  if(value==1){
    redDeploy();
  }
  else if(value==2){
    greenDeploy();
  }
}

// Function to get starting positions
void startPaddle(int value){
  if(value==1){
    digitalWrite(dirPin, LOW);
    while(digitalRead(leftStop)) runMotor();
    Serial.println("left");
  }else if(value==2){
    digitalWrite(dirPin, HIGH);
    while(digitalRead(rightStop)) runMotor();
    Serial.println("right");
  }
}

///////////////////////////////////////////////////////////////////

void setup()
{
	Serial.begin(115200);
  while(!Serial);

  pinMode(ir_red, INPUT);
  pinMode(ir_green, INPUT);
  pinMode(stepPin, OUTPUT);
  pinMode(dirPin, OUTPUT);
  pinMode(relay, OUTPUT);
  pinMode(leftMove, INPUT_PULLUP); 
  pinMode(rightMove, INPUT_PULLUP); 
  pinMode(rightStop, INPUT_PULLUP); 
  pinMode(leftStop, INPUT_PULLUP); 
  pinMode(solenoid, INPUT_PULLUP); 
  pinMode(buzzer, OUTPUT);

  digitalWrite(relay, HIGH); // switch off relay at first

  lift_green.attach(14);  // Attaches the servo object 'lift_green' to pin 10
  push_green.attach(15);   // Attaches the servo object 'push_green' to pin 9
  push_green.write(10);   // Initialize push_green servo to starting position
  lift_green.write(90);

  lift_red.attach(50);  // Attaches the servo object 'lift_red' to pin 10
  push_red.attach(52);   // Attaches the servo object 'push_red' to pin 9
  lift_red.write(90);

  lcd_gameSetup.begin();
	lcd_gameSetup.backlight();
  lcd_green.begin();
	lcd_green.backlight();
  lcd_red.begin();
	lcd_red.backlight();

  lcd_green.setCursor(4,0);
  lcd_green.print("DualPlay");
  lcd_red.setCursor(4,0);
  lcd_red.print("DualPlay");

  // wait until for the signal from raspberry pi (to identify the correct port)
  String s;
  while(!(Serial.available()>0)){
    if(Serial.available()>0){
      s = Serial.readStringUntil('\n');
      if(s=='port'){
        break;
      }
    }
    lcd_gameSetup.setCursor(0,0);
    lcd_gameSetup.print("Loading....");
  }

  ClearSerial();

  // send a signal to raspberry pi to get and distiguish the correct port of mega and uno
  delay(500);
  Serial.println("1");
}

void loop()
{

  lcd_green.setCursor(4,0);
  lcd_green.print("DualPlay");
  lcd_red.setCursor(4,0);
  lcd_red.print("DualPlay");

	// Wait until for the signal from the Raspberry pi
  String start;
  while (true){
    if(Serial.available() > 0){
        start = Serial.readStringUntil('\n');
        if(start=="start"){
          break;
        }
    }
  }
  ClearSerial();
  gameSetup();
  delay(1000);

  Serial.println(com);
  delay(1000);

  if(com==0){
    // stop executing code if they selected switch off
    while(true);
  }

  lcd_green.clear();
  lcd_red.clear();

  // check the ball is in a hole or not to start the game
  while(true){
    ir_value = breakbeam();
    if(ir_value){
      break;
    }
    lcd_green.setCursor(0,0);
    lcd_green.print("Insert the ball");
    lcd_green.setCursor(0,1);
    lcd_green.print("to a hole!!");
    lcd_red.setCursor(0,0);
    lcd_red.print("Insert the ball");
    lcd_red.setCursor(0,1);
    lcd_red.print("to a hole!!");
  }

  delay(1500);

  lcd_green.clear();
  lcd_red.clear();

  delay(400);

  lcd_green.setCursor(0, 0);
  lcd_green.print("Game is starting");
  lcd_red.setCursor(0, 0);
  lcd_red.print("Game is starting");
  scoreDisplay(0,0);
  
  // get the starting position of two paddles
  startPaddle(ir_value);

  delay(1500);

  lcd_green.clear();
  lcd_red.clear();

  delay(500);

  // initial score
  lcd_green.setCursor(0, 0);
  lcd_green.print("Score Update:");
  lcd_red.setCursor(0, 0);
  lcd_red.print("Score Update:");
  scoreDisplay(0,0);

  // code to lift the ball and strike to the play area
  redeploy(ir_value);

  delay(500);
  
  // send a signal to raspberry pi to start the game
  Serial.println("100");

  ir_value = 0;

  // loop to run until one player wins
  while(true){
    // code to run paddle according to the user input until a beam breaks(until ball go to a hole)
    while(!ir_value){
      ir_value = breakbeam();
      currentTime = millis();
      handleButtons();
      handleSolenoid();
    }
    sound_buzzer();
    ClearSerial();
    delay(100);
    // send a message to tell raspberry pi to stop the remote/AI functions
    Serial.print("6");
    delay(1000);

    // update scores
    score_update(ir_value);

    // get the starting positions
    startPaddle(ir_value);

    delay(2000);

    // end the game if one player wins
    if(greenScore== Nrounds || redScore==Nrounds){
      Serial.print("8");
      break;
    }
  
    delay(1000);

    // code to lift the ball and strike to the play area
    redeploy(ir_value);
    Serial.print("7");

    ir_value = 0;
  }

  if(greenScore == Nrounds){
    lcd_green.setCursor(0,0);
    lcd_green.print("Woo-hoo-You Won!");
    lcd_green.setCursor(0,1);
    lcd_green.print("easy right? :)");
    lcd_red.setCursor(0,0);
    lcd_red.print("Game over :(");
    lcd_red.setCursor(0,1);
    lcd_red.print("Until Next Time");

    lcd_gameSetup.clear();
    lcd_gameSetup.setCursor(0,0);
    lcd_gameSetup.print("Player Green");
    lcd_gameSetup.setCursor(0,1);
    lcd_gameSetup.print("Won The Match !!");
  }
  else if(redScore == Nrounds){
    lcd_red.setCursor(0,0);
    lcd_red.print("Woo-hoo-You Won!");
    lcd_red.setCursor(0,1);
    lcd_red.print("easy right? :)");
    lcd_green.setCursor(0,0);
    lcd_green.print("Game over :(");
    lcd_green.setCursor(0,1);
    lcd_green.print("Until Next Time");

    lcd_gameSetup.clear();
    lcd_gameSetup.setCursor(0,0);
    lcd_gameSetup.print("Player red");
    lcd_gameSetup.setCursor(0,1);
    lcd_gameSetup.print("Won The Match !!");
  }

  delay(15000);
  lcd_green.clear();
  lcd_red.clear();
  lcd_gameSetup.clear();
  greenScore = 0;
  redScore = 0;
}

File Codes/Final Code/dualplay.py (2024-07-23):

# DualPlay
# Code for raspberry pi

import serial
import time
import os
import cv2
import numpy as np
import pygame

pygame.mixer.init()


# Setup Camera
cap = cv2.VideoCapture(0)
cap.set(3, 600)
cap.set(4, 640)

color_ball = [27, 176, 138]# Color in BGR colorspace
color_paddle = [0,0,255] 
#color_paddle = [23,0,147]
#color_paddle = [0,0,166] 

# Variables to get the mid point of the ball and the paddle
# center_x = center_y = center_xp = center_xy = 0
# But here we use coners of identified colors (ball and paddle) to get the location

# Define serial connections
arduino1 = serial.Serial('/dev/ttyACM0', 115200, timeout=1)
arduino2 = serial.Serial('/dev/ttyACM1', 115200, timeout=1)

# Define variables to identify the correct ports
port = 0
# port = 1 means arduino1 is the arduino mega (human play)
# port = 2 means arduino2 is the arduino mega (human play)

# reset serial buffer
arduino1.reset_input_buffer()
arduino2.reset_input_buffer()

# Send a message to start the program
time.sleep(2)
arduino1.write(b'port')
arduino2.write(b'port')

# loop to get the feedback from the arduino and identify the correct port 
while True :
    if arduino1.in_waiting > 0:
        com = arduino1.readline().decode('utf-8').rstrip()
        arduino1.reset_input_buffer()
        port = 1 
        break

    if arduino2.in_waiting > 0:
        com = arduino2.readline().decode('utf-8').rstrip()
        arduino2.reset_input_buffer()
        port = 2
        break 

def get_limits(color):
    c = np.uint8([[color]])  # BGR values
    hsvC = cv2.cvtColor(c, cv2.COLOR_BGR2HSV)
    
    hue = hsvC[0][0][0]  # Get the hue value

    # Handle red hue wrap-around
    if hue >= 165:  # Upper limit for divided red hue
        lowerLimit = np.array([hue - 10, 100, 100], dtype=np.uint8)
        upperLimit = np.array([180, 255, 255], dtype=np.uint8)
    elif hue <= 15:  # Lower limit for divided red hue
        lowerLimit = np.array([0, 100, 100], dtype=np.uint8)
        upperLimit = np.array([hue + 10, 255, 255], dtype=np.uint8)
    else:
        lowerLimit = np.array([hue - 10, 100, 100], dtype=np.uint8)
        upperLimit = np.array([hue + 10, 255, 255], dtype=np.uint8)

    return lowerLimit, upperLimit


# Function to send a message to arduino mega
def sendMega(msg):
    global port
    if port==1:
        arduino1.write(f"{msg}\n".encode())
    else:
        arduino2.write(f"{msg}\n".encode())
        
    time.sleep(0.01)

# Function to send a message to arduino Uno
def sendUno(msg):
    global port
    if port==1:
        arduino2.write(f"{msg}\n".encode())
    else:
        arduino1.write(f"{msg}\n".encode())
    
    time.sleep(0.01)

# Function to get data from arduino Mega
def getMega():
    com = None
    if port==1:
        while True :
            if arduino1.in_waiting > 0:
                com = arduino1.readline().decode('utf-8').rstrip()
                arduino1.reset_input_buffer() 
                break
    else:
        while True:
            if arduino2.in_waiting > 0:
                com = arduino2.readline().decode('utf-8').rstrip()
                arduino2.reset_input_buffer()
                break
    return com

# Function to get data from arduino Mega without waiting
def _getMega():
    com = None
    if port==1:
        if arduino1.in_waiting > 0:
            com = arduino1.readline().decode('utf-8').rstrip()
            arduino1.reset_input_buffer() 
    else:
        if arduino2.in_waiting > 0:
            com = arduino2.readline().decode('utf-8').rstrip()
            arduino2.reset_input_buffer()
            
    return com

def tracking():
    global cap
    
    arduino1.reset_input_buffer()
    arduino2.reset_input_buffer()
    
    x = y = w = h = xp = yp = wp = hp = 0
    while True:
        ret, frame = cap.read() #Get frames

        hsvImage = cv2.cvtColor(frame, cv2.COLOR_BGR2HSV) #Convert into HSV

        lowerLimit_ball, upperLimit_ball = get_limits(color_ball) #Get the range of the color that need to identify
        lowerLimit_paddle, upperLimit_paddle = get_limits(color_paddle)

        mask_ball = cv2.inRange(hsvImage, lowerLimit_ball, upperLimit_ball) #Create a mask (If the color is identified - white, other locations black)
        mask_paddle = cv2.inRange(hsvImage, lowerLimit_paddle, upperLimit_paddle)

        contours_ball, gg = cv2.findContours(mask_ball, cv2.RETR_EXTERNAL, cv2.CHAIN_APPROX_SIMPLE) #Find those white signs
        contours_paddle, gg1 = cv2.findContours(mask_paddle, cv2.RETR_EXTERNAL, cv2.CHAIN_APPROX_SIMPLE) 
        #cv2.imshow('c', mask_ball)
        
        for contour in contours_ball:
            area = cv2.contourArea(contour) #Find the area of each contour
            if area > 100:  # Adjust the area threshold as needed
                x, y, w, h = cv2.boundingRect(contour) #Get the location as a rectangle
                #cv2.drawContours(frame, contour, -1, (0,255,0), 1)
                cv2.rectangle(frame, (x, y), (x + w, y + h), (0, 255, 0), 5) 
                #center_x = x + w // 2
                #center_y = y + h // 2
                print(f"ball: ({y}, {yp})")
                
        for contour in contours_paddle:
            areap = cv2.contourArea(contour) #Find the area of each contour
            if areap > 500:  # Adjust the area threshold as needed
                xp, yp, wp, hp = cv2.boundingRect(contour) #Get the location as a rectangle
                #cv2.drawContours(frame, contour, -1, (0,255,0), 1)
                cv2.rectangle(frame, (xp, yp), (xp + wp, yp + hp), (255, 0, 0), 5) 
                #center_xp = xp + wp // 2
                #center_yp = yp + hp // 2
                print(f"paddle: ({xp}, {xp+wp})")
                
        if x < xp+33 and (y-yp-hp)>=-40:
                print(0)
                sendUno('0\n')
                
        elif x+w > xp+wp-33 and (y-yp-hp)>=-40:
                print(1)
                sendUno('1\n')
                
        elif (x>= xp+33 ) and ((x+w)<=(xp+wp-33)):
                print(-1)
                sendUno('-1\n')
           
            
        if 30>=(y-yp-hp)>=-20 and ((x+w) >= xp) and ((x)<=(xp+wp)):
            sendUno("2\n")
            print(10)
            
               
        cv2.imshow('frame', frame)
        
        if cv2.waitKey(1) and _getMega()=="6":
            sendUno('10')
            cv2.destroyAllWindows()
            break
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

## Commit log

2024-03-29 project on 30/3/2024
    [Gantt chart.xlsx]
2024-05-01 Added and modified files and folders.
    [Display_and_Keypad_Cover.stl, RACK_V2.stl, Servo_mount_V2.stl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]
2024-07-23 Finalize Folders and Files
    [Assem1.SLDASM, Display_and_Keypad_Cover.stl, Gantt chart.xlsx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]
